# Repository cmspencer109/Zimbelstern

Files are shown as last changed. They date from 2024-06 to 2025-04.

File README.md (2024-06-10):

# The St. Martin Luther Zimbelstern

A MIDI-enabled zimbelstern for organs without one.

<div style="display: flex; justify-content: space-between;">
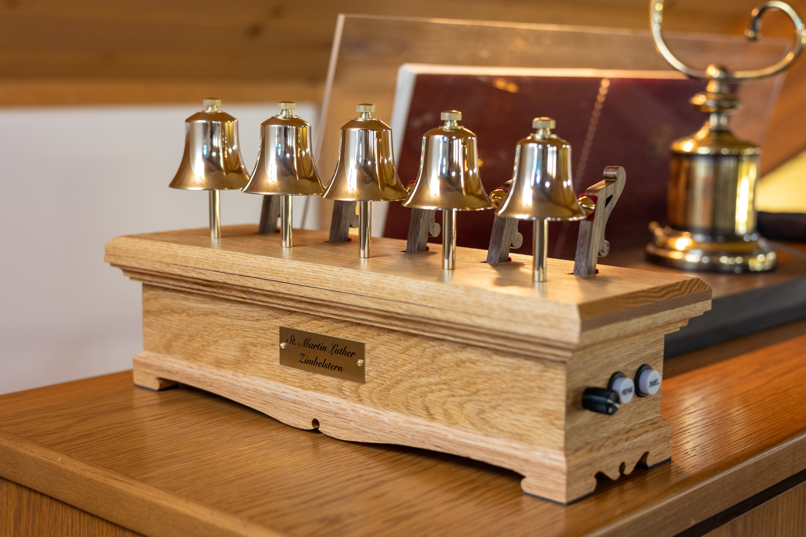
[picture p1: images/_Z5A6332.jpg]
  
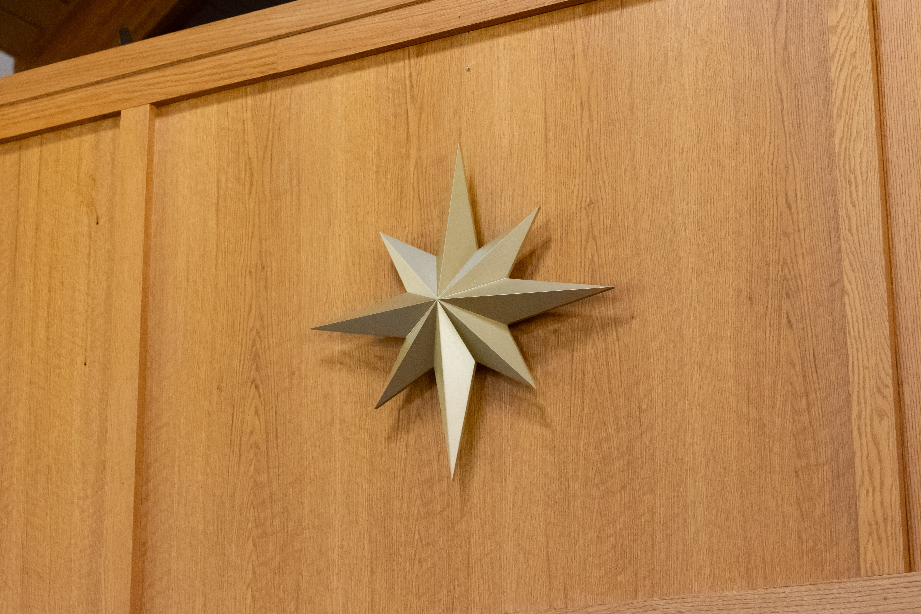
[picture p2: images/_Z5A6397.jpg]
   
</div>
<br>
This repo contains the code, schematics, and cad design files for the St. Martin Luther Zimbelstern.

## Design Overview

The St. Martin Luther Zimbelstern is an instrument designed for organs without a zimbelstern built into them. It features a solid oak case which fits comfortably on top of the organ console, allowing the controls to be in easy reach of the organist. In addition to a traditional Zimbel button for starting and stopping the zimbelstern, the St. Martin Luther Zimbelstern features a Prepare button which, when connected to a supported organ via MIDI, can identify when an organist begins playing the keyboards and automatically starts the zimbelstern.

Unlike more traditional designs which employ a rotating mechanism to strike a series of bells, this design allows for each bell to be played individually. Each bell is struck with a hammer which is actuated with an electromagnet. This allows the bells to be played at random, rather than in a predefined repeating sequence, as well as allowing adjustment over the speed and volume of the ringing. The electromagnets are controlled by a Raspberry Pi Pico microcontroller which lies at the heart of the zimbelstern, and is responsible for the entire operation of the zimbelstern.

The instrument uses 5 tuned Malmark handbells which form the D minor pentatonic scale. The pitches are D7, F7, G7, A7, and C8.

### MIDI Integration

The St. Martin Luther Zimbelstern has a MIDI IN port which can be connected to the MIDI OUT on a supported organ. The MIDI connection is only one-way, which means the zimbelstern only listens to the organ and does not talk back.

The MIDI connection is used for the Prepare button, which, when engaged will listen for "Note On" MIDI messages from the organ. When one of these messages is received, the microcontroller knows the organist has begun playing and will automatically start the zimbelstern.

Additionally, the MIDI connection is used to determine if any stops are engaged on the organ. This way, if the organist has pressed the Prepare button on the zimbelstern, but not yet engaged a registration on the organ, the zimbelstern will not start from an accidental silent key press. This functionality reads System Exclusive MIDI messages to identify if any stops are activated*, however, these are unique per organ manufacturer. As a result, the Prepare button will only work on Rodgers organs or any organ that uses the Rodgers/Roland SysEx message format. Support for other organs can be added by adding logic to read their SysEx message format.

*If the zimbelstern is plugged in after the organ is turned on, a stop change needs to be made on the organ to trigger a SysEx message so the zimbelstern can know the current state of the organ.

## Electronics

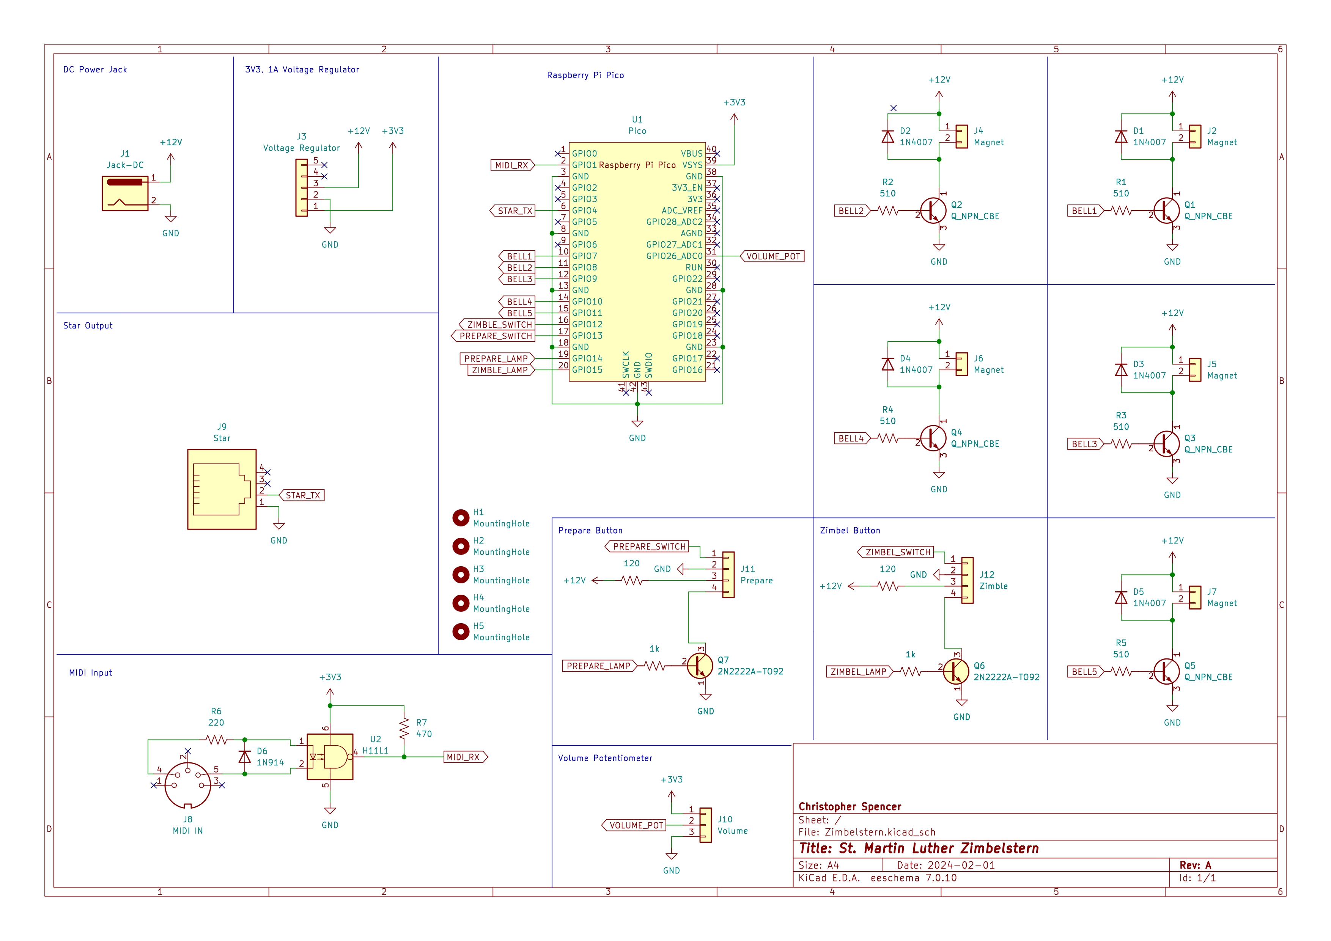
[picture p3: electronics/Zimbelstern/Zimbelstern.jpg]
Zimbelstern Schematic


### Circuit Board

* [JLCPCB](https://jlcpcb.com/) was used to order the PCB. The folder `Zimbel-2024-03-03` contains a KiCad export of all the files needed to order a new board from a PCB fabricator.

## Meaning Behind the Name

The name "St. Martin Luther Zimbelstern" reflects several key points about this zimbelstern. It is named after the great reformer Martin Luther who is remembered as we celebrate various 500-year anniversaries of Luther's work during the time of the reformation. Second, since the sound of the zimbelstern often signifies the song of heaven, the additional title of "St." reminds us that we are joined with Martin Luther and all those who are saints in heaven by Jesus' blood. Third, this zimbelstern was designed and built specifically for Martin Luther Church in Sunset Hills, Missouri whose name is also reflected in this name.

## Known Design Flaws

This zimbelstern was developed rapidly over 6 months and has some flaws. Below is a list of things that should be improved in future versions:

* Hammers produce an undesirable clacking sound when striking the bell
  * This is caused by a number of reasons, and may not be fixable without changing the hammer mechanism entirely.
  * The clearest bell rings occur when the striking object makes contact for the shortest amount of time possible. The longer the striking object remains on the bell, the more muted the tone will become until it doesn't ring at all. This is the first issue. The electromagnets cannot move the hammers fast enough. One solution is to reduce the weight of the hammers so they can swing faster. A better solution would be to use a mechanism similar to a grandfather clock, where the hammer is pulled back and springs forward to strike the bell.
  * The second issue is that the wooden hammer is absorbing some of the vibrations when striking and the wood is producing a dull echoing sound. Loosening the brass hammer head and adding a felt pad between the wooden hammer has helped to reduce this, but does not solve it entirely. One solution is to build the hammers out of a different material, such as all brass.
* ZIMBEL piston lamp voltage not properly regulated
  * The piston lamps operate at 5v, and are said to be used with a series resistor in Rodgers organs. This same type of series resistor configuration was used in the zimbelstern circuit to reduce the main 12v source to 5v. However, since the electromagnets also draw from the main 12v source a flickering in the piston lamp is produced when the zimbelstern is ringing.
  * One solution is to properly regulate the 12v to 5v using a buck converter. In the production model, the series resistor was removed and an extra buck converter wired in place. A proper fix would build this into the PCB.

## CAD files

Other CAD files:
electronics/Zimbelstern/KiCad-RP-Pico/SketchUp Model/Pico.skp
fusion360/P25-20 Bracket.f3d
fusion360/Pot Shaft Extender.f3d
fusion360/Potentiometer Bracket.f3d
fusion360/Rod Mount.f3d
fusion360/Star Motor Mount.f3d
fusion360/Star.f3d

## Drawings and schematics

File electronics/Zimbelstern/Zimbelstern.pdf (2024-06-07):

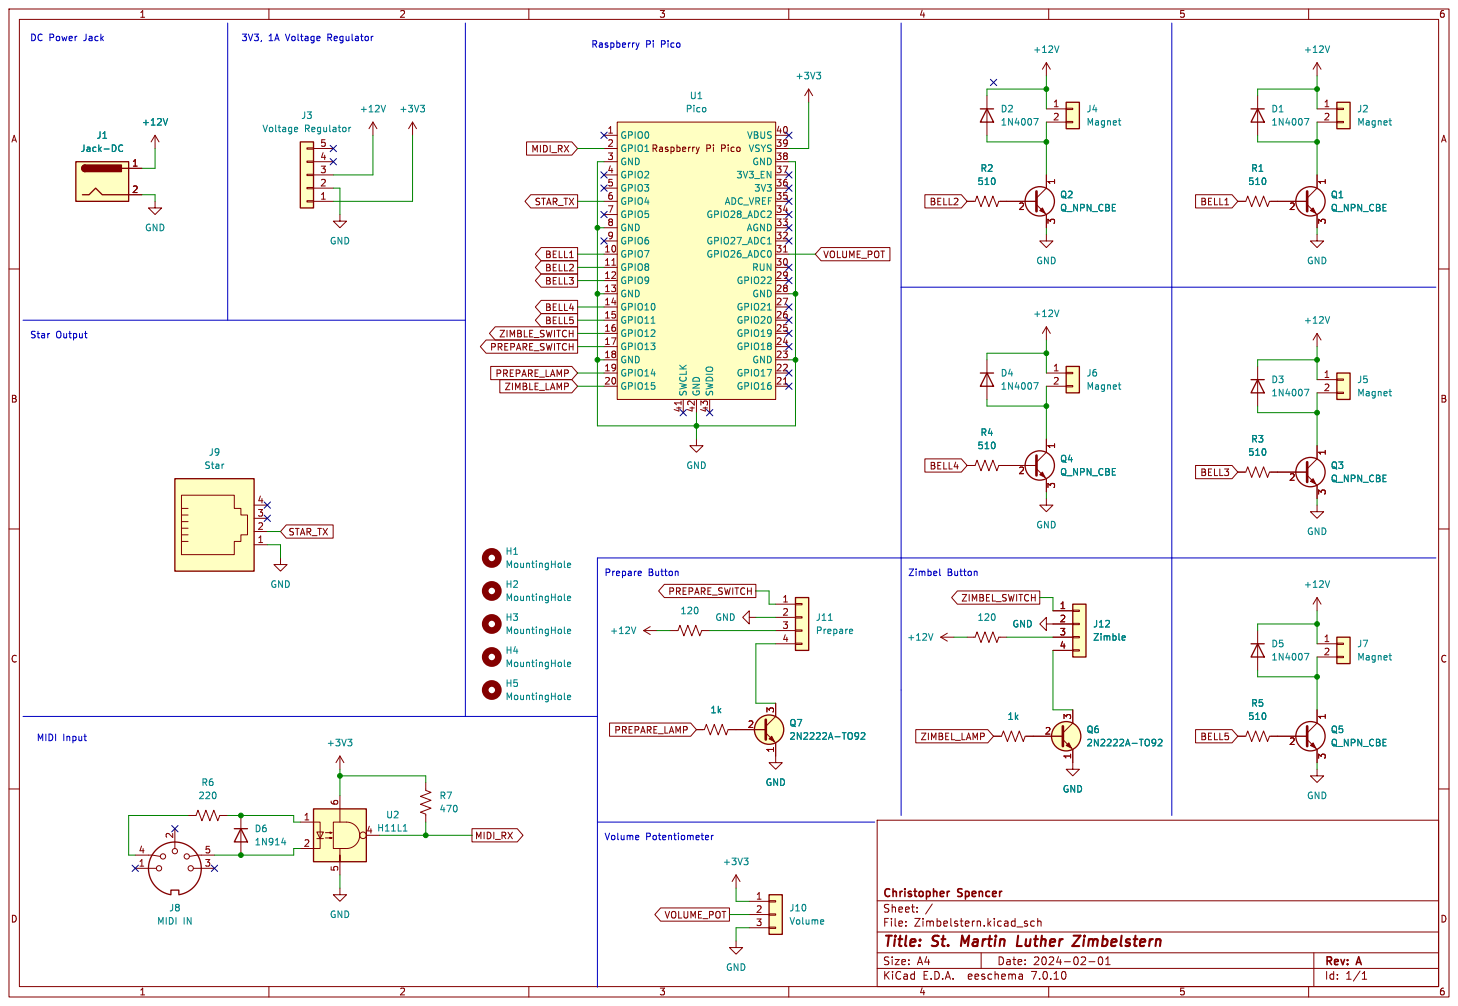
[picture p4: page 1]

3V3, 1A Voltage Regulator Star Output

File: Zimbelstern.kicad_sch Sheet: / Christopher Spencer GND

Volume Potentiometer MIDI Input

Id: 1/1 Title: St. Martin Luther Zimbelstern

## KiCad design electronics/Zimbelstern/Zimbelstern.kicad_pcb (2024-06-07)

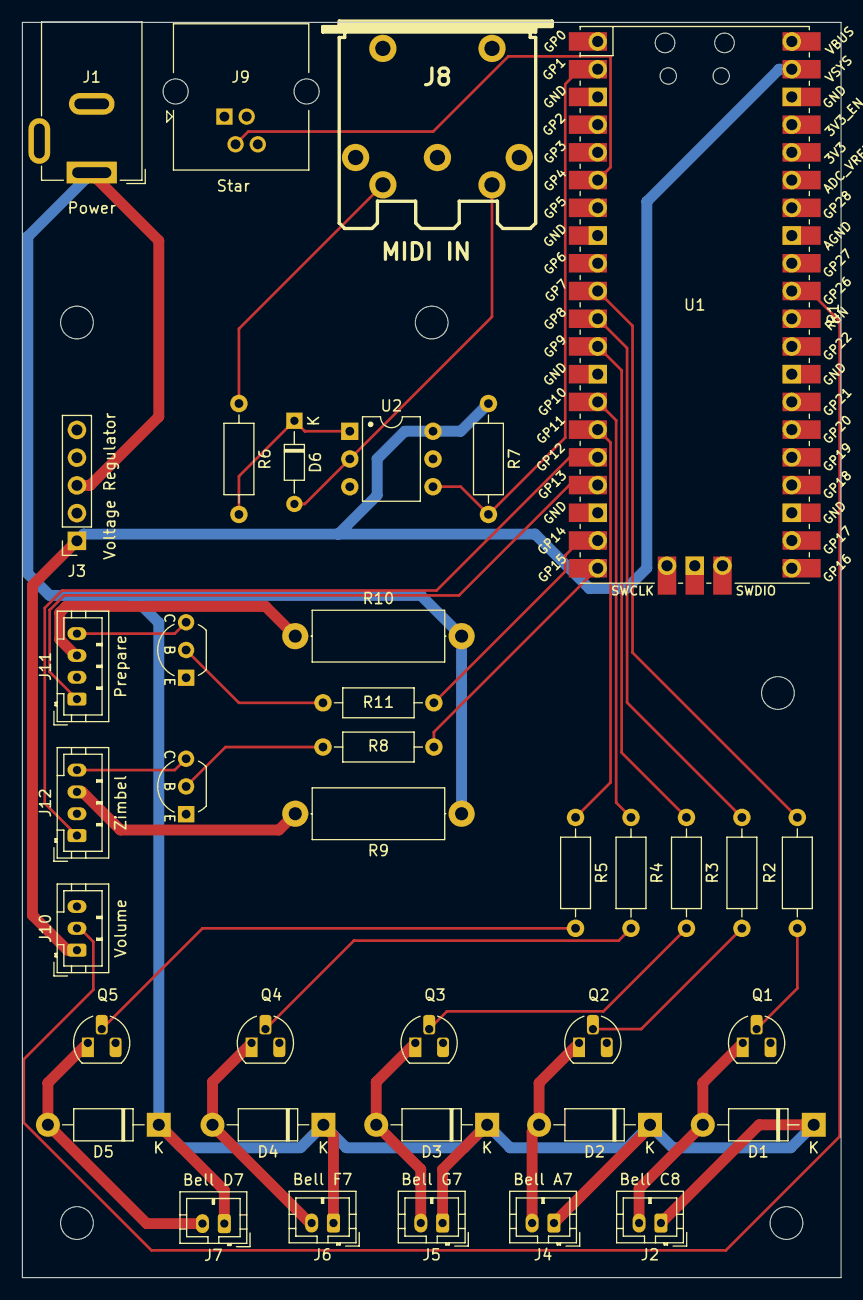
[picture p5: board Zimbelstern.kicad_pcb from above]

Board: 2 copper layers, 75.0 x 115.0 mm, 43 parts (0 on the bottom side), 34 nets.

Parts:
D1, D2, D3, D4, D5: 1N4007; D_DO-41_SOD81_P10.16mm_Horizontal
D6: 1N914; D_DO-34_SOD68_P7.62mm_Horizontal
H1, H2, H3, H4, H5: MountingHole; MountingHole_3mm
J1: Power; BarrelJack_GCT_DCJ200-10-A_Horizontal
J2: Bell C8; JST_PH_B2B-PH-K_1x02_P2.00mm_Vertical
J3: Voltage Regulator; PinSocket_1x05_P2.54mm_Vertical
J4: Bell A7; JST_PH_B2B-PH-K_1x02_P2.00mm_Vertical
J5: Bell G7; JST_PH_B2B-PH-K_1x02_P2.00mm_Vertical
J6: Bell F7; JST_PH_B2B-PH-K_1x02_P2.00mm_Vertical
J7: Bell D7; JST_PH_B2B-PH-K_1x02_P2.00mm_Vertical
J8: MIDI IN; MIDI_DIN5
J9: Star; RJ14_Connfly_DS1133-S4_Horizontal
J10: Volume; JST_PH_B3B-PH-K_1x03_P2.00mm_Vertical
J11: Prepare; JST_PH_B4B-PH-K_1x04_P2.00mm_Vertical
J12: Zimbel; JST_PH_B4B-PH-K_1x04_P2.00mm_Vertical
Q1, Q2, Q3, Q4, Q5: Q_NPN_CBE; TO-92_HandSolder
Q6, Q7: 2N2222A-TO92; TO-92_Inline_Wide_EBC
R1, R2, R3, R4, R5: 510; R_Axial_DIN0207_L6.3mm_D2.5mm_P10.16mm_Horizontal
R6: 220; R_Axial_DIN0207_L6.3mm_D2.5mm_P10.16mm_Horizontal
R7: 470; R_Axial_DIN0207_L6.3mm_D2.5mm_P10.16mm_Horizontal
R8, R11: 1k; R_Axial_DIN0207_L6.3mm_D2.5mm_P10.16mm_Horizontal
R9, R10: 120; R_Axial_DIN0414_L11.9mm_D4.5mm_P15.24mm_Horizontal
U1: Pico; RPi_Pico_SMD_TH
U2: H11L1; DIP-6_W7.62mm

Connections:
+3V3: J3.1, J10.1, R7.1, U1.39 (VSYS), U2.6
+12V: D1.1 (K), D2.1 (K), D3.1 (K), D4.1 (K), D5.1 (K), J1.1, J2.1, J3.3, J4.1, J5.1, J6.1, J7.1, R9.1, R10.1
BELL1: R1.1, U1.10 (GPIO7)
BELL2: R2.1, U1.11 (GPIO8)
BELL3: R3.1, U1.12 (GPIO9)
BELL4: R4.1, U1.14 (GPIO10)
BELL5: R5.1, U1.15 (GPIO11)
GND: J1.2, J3.2, J9.1, J10.3, J11.2, J12.2, Q1.3 (E), Q2.3 (E), Q3.3 (E), Q4.3 (E), Q5.3 (E), Q6.1 (E), Q7.1 (E), U1.3 (GND), U1.8 (GND), U1.13 (GND), U1.18 (GND), U1.23 (GND), U1.28 (GND), U1.38 (GND), U1.42 (GND), U2.5
MIDI_RX: R7.2, U1.2 (GPIO1), U2.4
unnamed: D1.2 (A), J2.2, Q1.1 (C)
unnamed: D2.2 (A), J4.2, Q2.1 (C)
unnamed: D3.2 (A), J5.2, Q3.1 (C)
unnamed: D4.2 (A), J6.2, Q4.1 (C)
unnamed: D5.2 (A), J7.2, Q5.1 (C)
unnamed: D6.2 (A), J8.5, U2.2
unnamed: D6.1 (K), R6.2, U2.1
unnamed: J8.4, R6.1
unnamed: J11.3, R10.2
unnamed: J11.4, Q7.3 (C)
unnamed: J12.3, R9.2
unnamed: J12.4, Q6.3 (C)
unnamed: Q1.2 (B), R1.2
unnamed: Q2.2 (B), R2.2
unnamed: Q3.2 (B), R3.2
unnamed: Q4.2 (B), R4.2
unnamed: Q5.2 (B), R5.2
unnamed: Q6.2 (B), R8.2
unnamed: Q7.2 (B), R11.2
PREPARE_LAMP: R11.1, U1.19 (GPIO14)
PREPARE_SWITCH: J11.1, U1.17 (GPIO13)
STAR_TX: J9.2, U1.6 (GPIO4)
VOLUME_POT: J10.2, U1.31 (GPIO26_ADC0)
ZIMBLE_LAMP: R8.1, U1.20 (GPIO15)
ZIMBLE_SWITCH: J12.1, U1.16 (GPIO12)

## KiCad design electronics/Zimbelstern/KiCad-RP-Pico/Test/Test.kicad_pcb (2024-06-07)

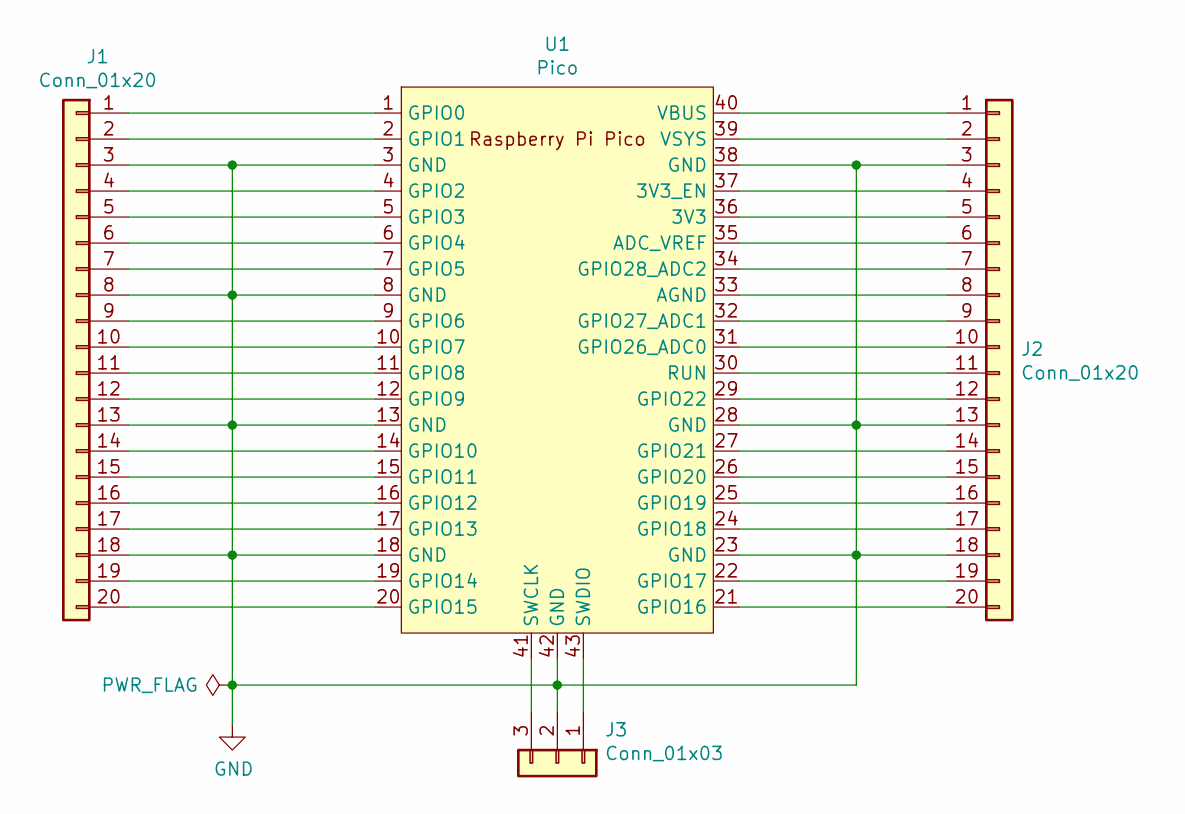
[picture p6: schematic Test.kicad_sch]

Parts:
J1, J2: Conn_01x20; PinSocket_1x20_P1.00mm_Vertical
J3: Conn_01x03; PinSocket_1x03_P1.00mm_Vertical
U1: Pico; RPi_Pico_SMD_TH

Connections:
GND: J1.3, J1.8, J1.13, J1.18, J2.3, J2.13, J2.18, J3.2, U1.3 (GND), U1.8 (GND), U1.13 (GND), U1.18 (GND), U1.23 (GND), U1.28 (GND), U1.38 (GND), U1.42 (GND)
unnamed: J1.1, U1.1 (GPIO0)
unnamed: J1.2, U1.2 (GPIO1)
unnamed: J1.4, U1.4 (GPIO2)
unnamed: J1.5, U1.5 (GPIO3)
unnamed: J1.6, U1.6 (GPIO4)
unnamed: J1.7, U1.7 (GPIO5)
unnamed: J1.9, U1.9 (GPIO6)
unnamed: J1.10, U1.10 (GPIO7)
unnamed: J1.11, U1.11 (GPIO8)
unnamed: J1.12, U1.12 (GPIO9)
unnamed: J1.14, U1.14 (GPIO10)
unnamed: J1.15, U1.15 (GPIO11)
unnamed: J1.16, U1.16 (GPIO12)
unnamed: J1.17, U1.17 (GPIO13)
unnamed: J1.19, U1.19 (GPIO14)
unnamed: J1.20, U1.20 (GPIO15)
unnamed: J2.1, U1.40 (VBUS)
unnamed: J2.2, U1.39 (VSYS)
unnamed: J2.4, U1.37 (3V3_EN)
unnamed: J2.5, U1.36 (3V3)
unnamed: J2.6, U1.35 (ADC_VREF)
unnamed: J2.7, U1.34 (GPIO28_ADC2)
unnamed: J2.8, U1.33 (AGND)
unnamed: J2.9, U1.32 (GPIO27_ADC1)
unnamed: J2.10, U1.31 (GPIO26_ADC0)
unnamed: J2.11, U1.30 (RUN)
unnamed: J2.12, U1.29 (GPIO22)
unnamed: J2.14, U1.27 (GPIO21)
unnamed: J2.15, U1.26 (GPIO20)
unnamed: J2.16, U1.25 (GPIO19)
unnamed: J2.17, U1.24 (GPIO18)
unnamed: J2.19, U1.22 (GPIO17)
unnamed: J2.20, U1.21 (GPIO16)
unnamed: J3.1, U1.43 (SWDIO)
unnamed: J3.3, U1.41 (SWCLK)

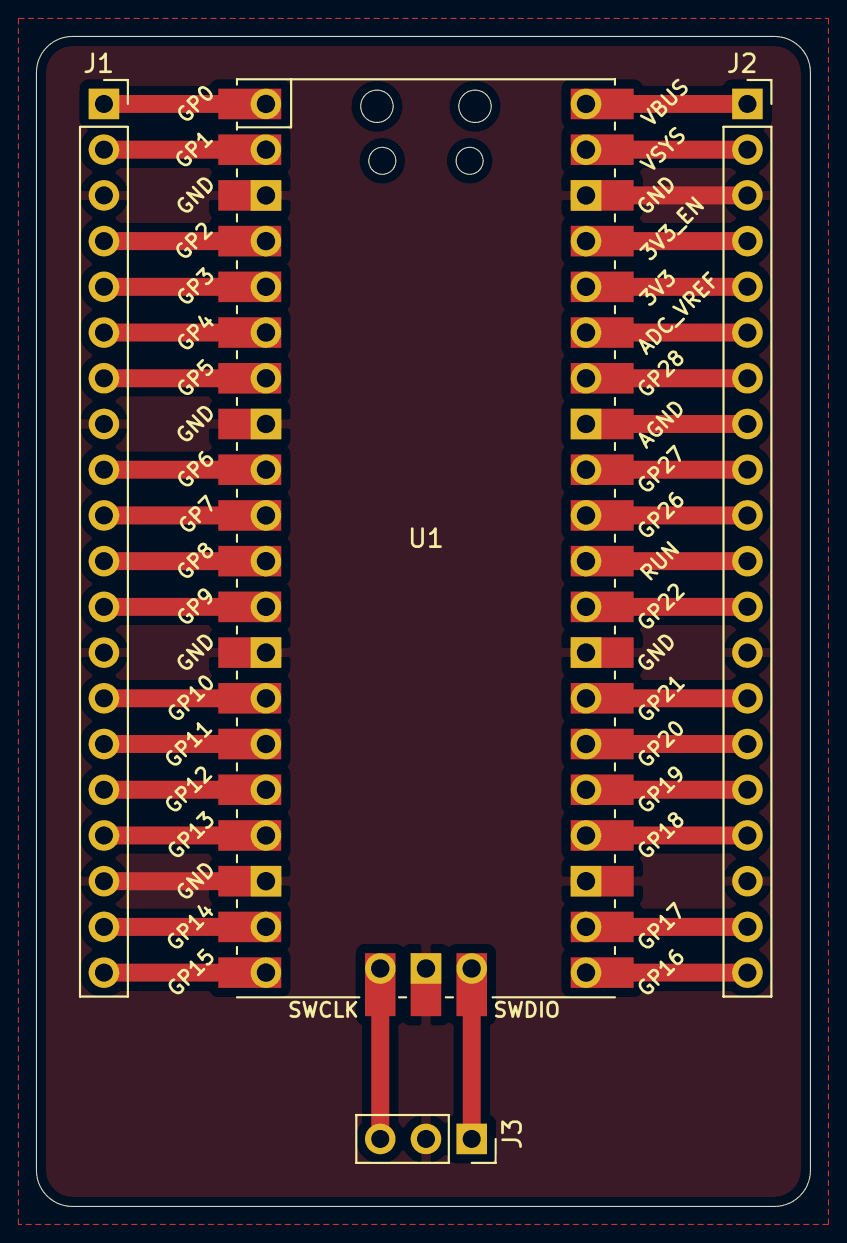
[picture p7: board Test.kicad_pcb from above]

Board: 2 copper layers, 43.0 x 65.0 mm, 4 parts (0 on the bottom side), 36 nets.

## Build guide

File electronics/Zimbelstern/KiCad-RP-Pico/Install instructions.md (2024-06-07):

# Install instructions

## 1. Copy the files locally

Copy the `RP-Pico Libraries` folder wherever you like on your computer.

## 2. Install the Raspberry Pi Pico board schema symbol

Use the `KiCad | Preferences | Manage Symbol Libraries...` command to manage the symbol library:

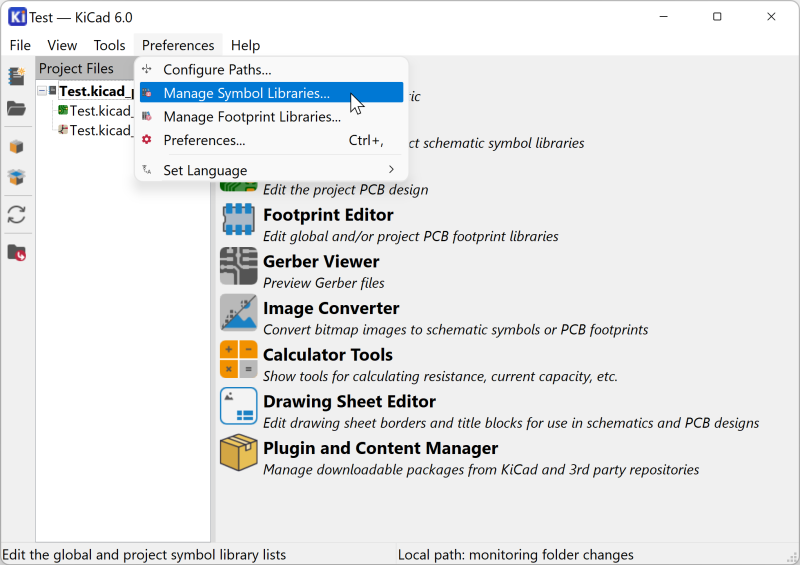
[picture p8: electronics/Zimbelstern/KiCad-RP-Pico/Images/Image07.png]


then select the global tab and click on the folder button:

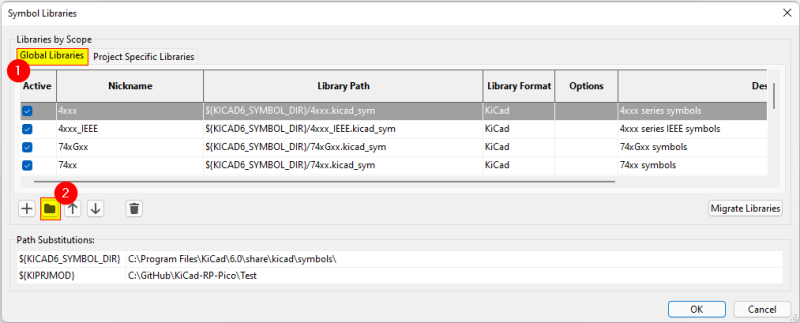
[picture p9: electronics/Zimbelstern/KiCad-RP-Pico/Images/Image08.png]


navigate to the `RP-Pico Libraries` folder, select the `MCU_RaspberryPi_and_Boards.kicad_sym` file and open it:

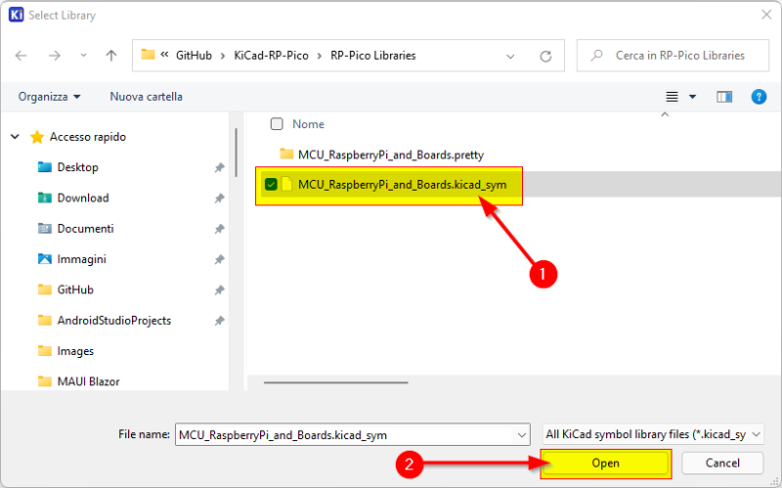
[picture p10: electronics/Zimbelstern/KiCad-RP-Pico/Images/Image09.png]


et voilà, the first step is completed:

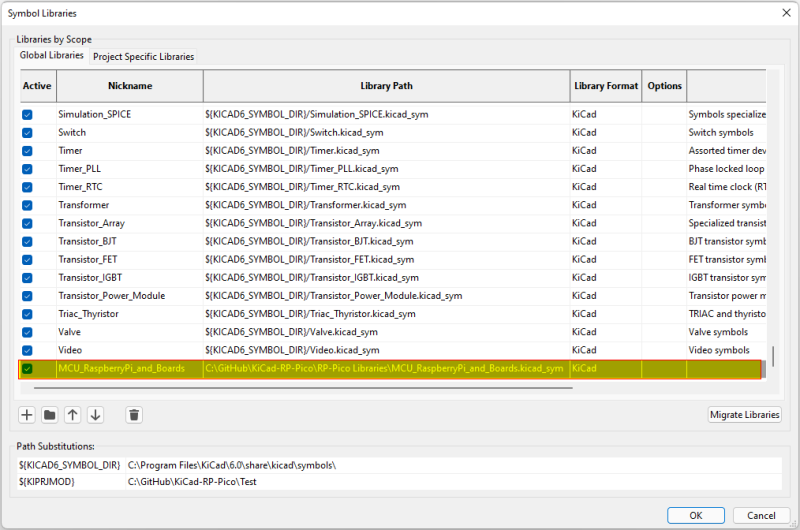
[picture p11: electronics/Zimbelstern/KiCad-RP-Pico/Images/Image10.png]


You can now close the symbol libraries manager window.

## 3. Install the Raspberry Pi Pico board footprint

You can use a similar approach to add the footprint to the footprint libraries manager, but I've found some issues that I've solved using the footprint editor, so here are the steps I suggest you to follow:

Open the footprint editor

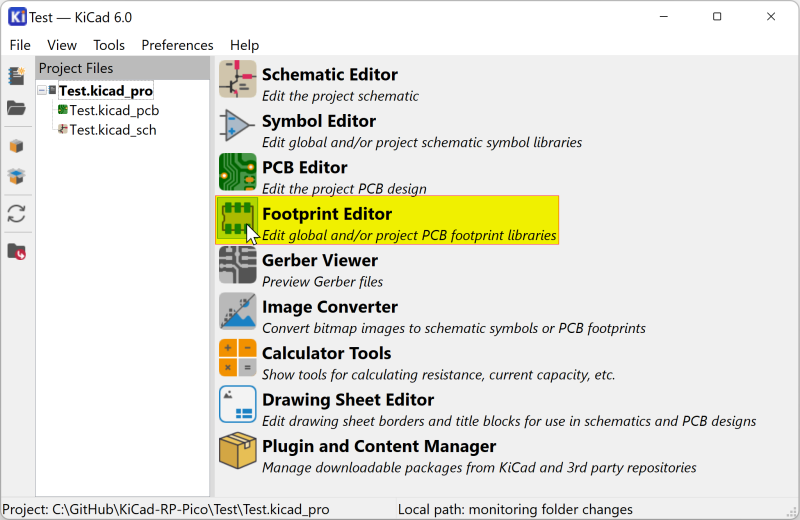
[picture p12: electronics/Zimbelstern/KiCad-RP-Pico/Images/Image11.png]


wait for the footprints to load... then use the `File | Add Library` command:

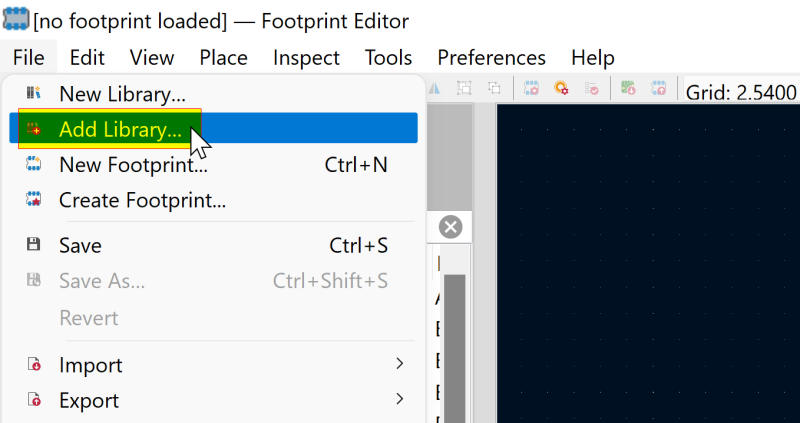
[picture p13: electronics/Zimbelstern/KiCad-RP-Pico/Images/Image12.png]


confirm the `Global` choice:

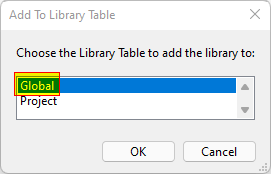
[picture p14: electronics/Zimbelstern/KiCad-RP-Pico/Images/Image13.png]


and select the `MCU_RaspberriPi_and_Boards.pretty` folder (yes, the folder represent a footprint library on KiCad):

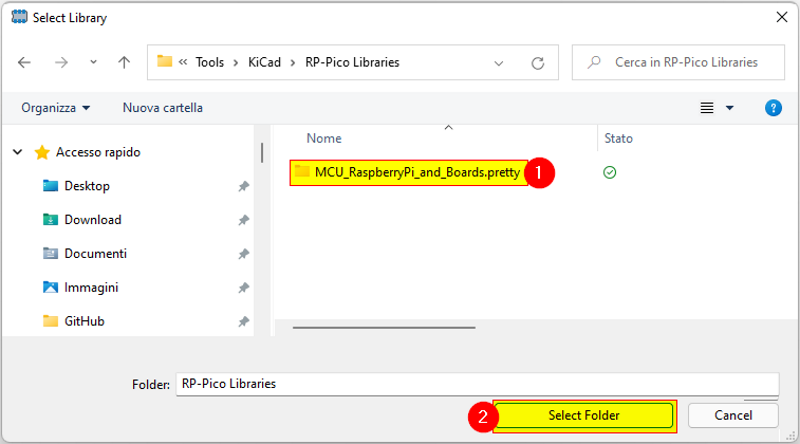
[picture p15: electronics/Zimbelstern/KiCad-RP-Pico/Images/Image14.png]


Now the library is installed on KiCad with the Raspberry Pi Pico footprint (double click on it to see it on the editor pane):

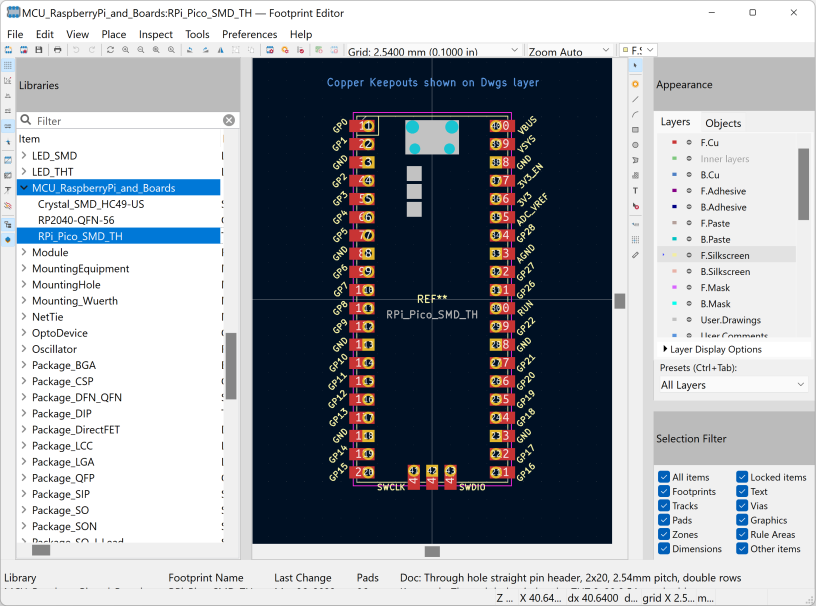
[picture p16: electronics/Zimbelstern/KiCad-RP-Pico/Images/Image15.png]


Don't close the windows as the next step start from here.

## 4. Install the Raspberry Pi Pico board footprint 3D visual

If not already open, open the the footprint editor

symbol library manager

double click on the `RPi_Pico_SMD_TH` footprint from the `MCU_RaspberriPi_and_Boards` library and then click on the `Footprint properties` icon:

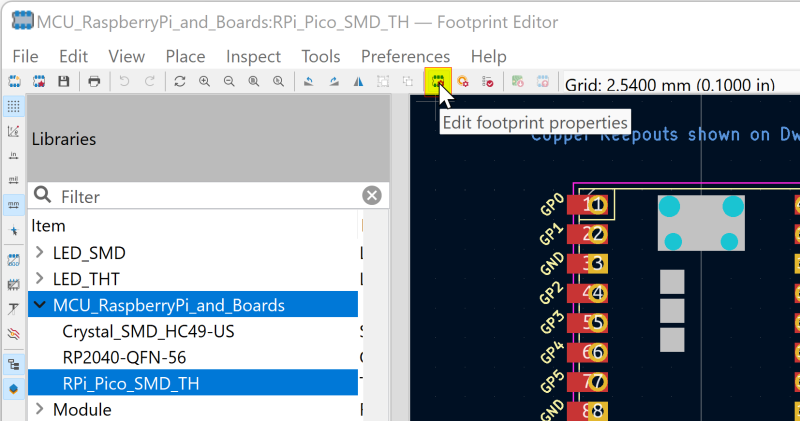
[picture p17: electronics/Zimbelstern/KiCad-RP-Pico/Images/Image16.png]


In the footprint properties window, first select the `3D Settings` tab. Please note that the preview shows only the PCB board with the footprint added on step 3, without any 3D representation of the Raspberry Pi Pico board. Now click on the folder icon to add the 3D model:

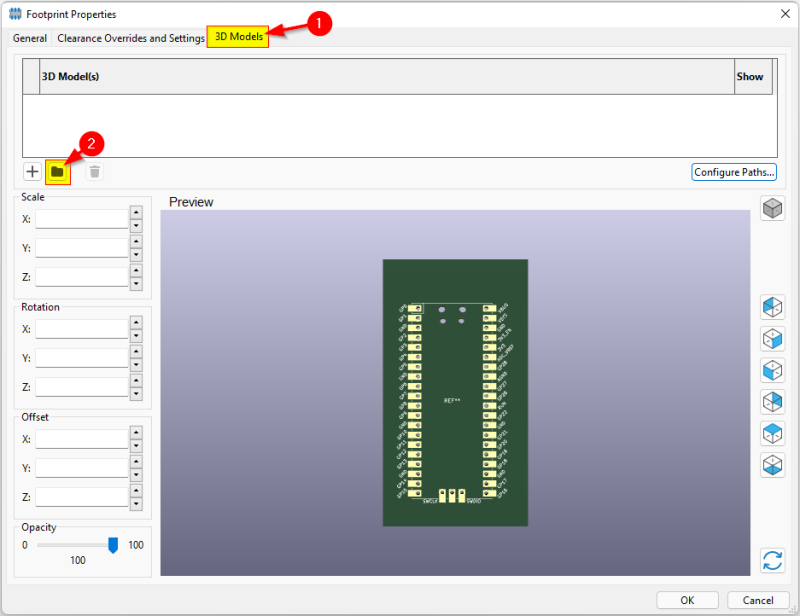
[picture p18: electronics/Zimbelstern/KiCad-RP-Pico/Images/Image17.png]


Navigate to the `RP-Pico Libraries` folder, select the `Pico.wrl` file and wait until the model is shown in the right panel, then confirm with OK:

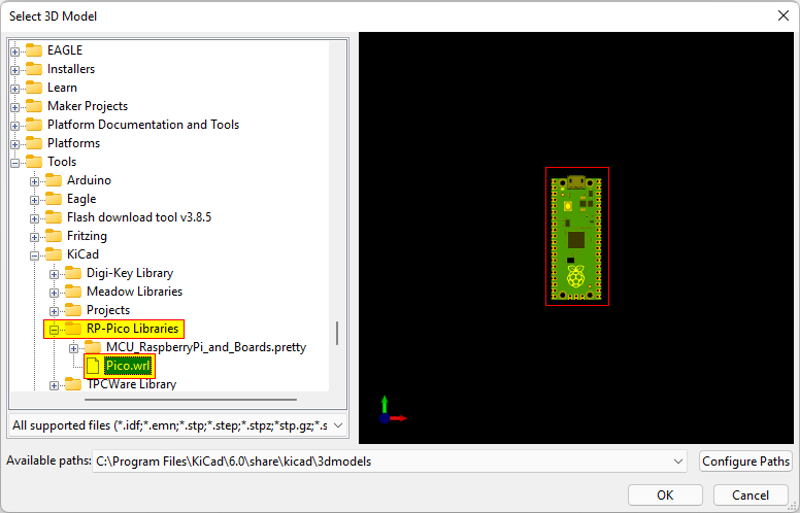
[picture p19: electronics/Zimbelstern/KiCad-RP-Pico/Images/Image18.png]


The model is already scaled and translated to match the footprint:

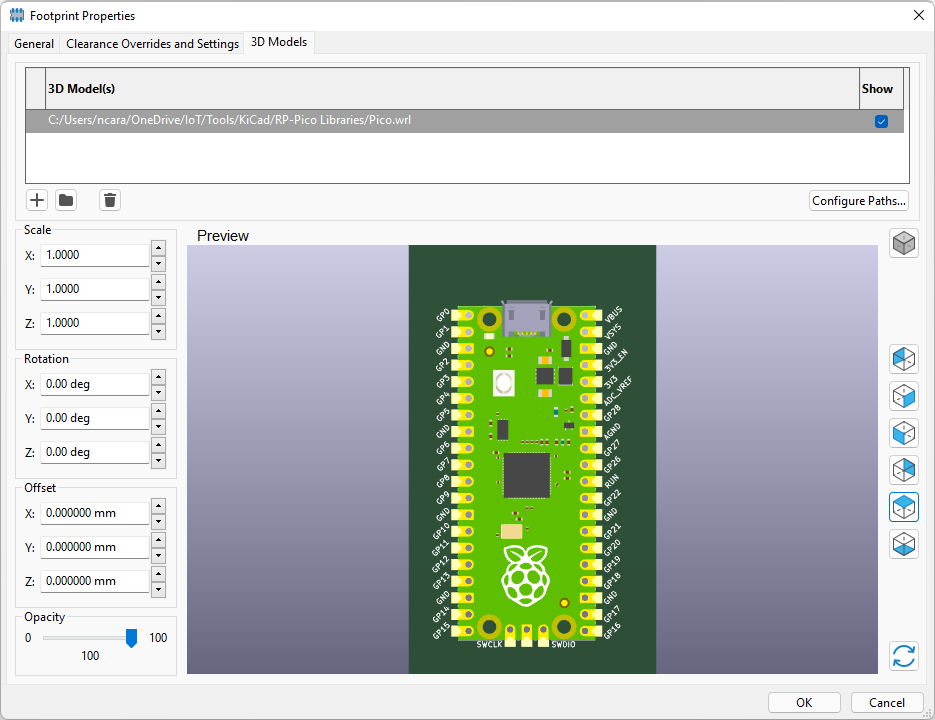
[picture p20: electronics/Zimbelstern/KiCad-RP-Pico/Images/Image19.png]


now close the `Footprint Properties` window, and the `Footprint Editor`, obviously saving the changes.

## Conclusion

Now that you've installed the schema and footprint and added the 3D model to the footprint, you can use the Raspberry Pi Pico board on your KiCad projects.

I've also added a test KiCad Project on the `Test` folder, that you can use to see an example of it.

Have fun!

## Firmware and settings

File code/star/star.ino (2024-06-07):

/*
The following program is intended for use with the Zimbelstern Star of Martin Luther Church, Sunset Hills, MO.
The program receives on and off communications, as well as speed values via a serial connection.

Bytes should be streamed to the device at minimum more than once per second. If the device does not receive communication 
after 1 second, it will shut off on its own. This is to prevent a runaway uncontrolled process in case of a connection failure.

Bytes are sent in hex form, where the upper nibble should be high (F) to indicate that it should turn on. 
The lower nibble 0 - F maps to the min and max speed constants defined below.

Examples:
0xF0 - Run at the slowest speed
0xF8 - Run at a medium speed
0xFF - Run at the maximum speed
0x00 - Doesn't do anything because the upper nibble is not high

*/

#include <AccelStepper.h>

// Define pins
#define ENABLE_PIN 2
#define STEP_PIN 3
#define DIRECTION_PIN 4

const int MIN_SPEED = 1000;
const int MAX_SPEED = 5000;
const int STARTING_ACCELERATION = 1000;
const int STOPPING_ACCELERATION = 750;

const int STEPS_IN_ONE_REVOLUTION = 6400; // 1600 steps * 4 pulley ratio

unsigned long lastByteReceivedTime = 0;
bool motorRunning = false;

AccelStepper stepper(AccelStepper::DRIVER, STEP_PIN, DIRECTION_PIN);

void setup() {
  // Set the pins
  pinMode(ENABLE_PIN, OUTPUT);
  pinMode(DIRECTION_PIN, OUTPUT);
  pinMode(STEP_PIN, OUTPUT);

  // Set the maximum speed and acceleration
  stepper.setMaxSpeed(MAX_SPEED);

  // Initialize Serial communication
  Serial.begin(9600);
}

void startMotor(int speed) {
  stepper.setAcceleration(STARTING_ACCELERATION);

  if (motorRunning == true) {
    return;
  }

  digitalWrite(ENABLE_PIN, LOW); // Low is on
  stepper.setMaxSpeed(speed);
  stepper.move(-2147483647); // Set the largest possible position. Multiply by -1 to change direction.
  motorRunning = true;
}

void stopMotor() {
  stepper.stop();
  motorRunning = false;
}

// Stops the motor on the closest quarter revolution with full deceleration
void stopMotorOnQuarter() {
  /* stepper.stop() updates the target position to the point at which it will stop
     based on the current speed and rate at which it will slow down.
     We then add to this number the smallest amount needed to make it divisble by
     the number of steps in a quarter revolution, and move to this new position.
  */
  stepper.setAcceleration(STOPPING_ACCELERATION);
  stepper.stop();
  long targetPosition = stepper.targetPosition();
  int stepsInQuarterRevolution = STEPS_IN_ONE_REVOLUTION / 4;
  long targetPositionToEndOnAQuarter = targetPosition - (stepsInQuarterRevolution + (targetPosition % -stepsInQuarterRevolution));
  stepper.moveTo(targetPositionToEndOnAQuarter);
  motorRunning = false;
}

void loop() {
  // Check if data is available on Serial
  if (Serial.available() > 0) {

    byte receivedByte = Serial.read();
    // Serial.println(receivedByte); // TESTING ONLY, DO NOT USE IN PRODUCTION

    // Extract upper nibble for control and lower nibble for speed
    byte control = (receivedByte & 0xF0) >> 4;
    byte speedValue = receivedByte & 0x0F;

    // Map 0 - F to the min and max speeds so sender can control the speed
    int speed = map(speedValue, 0, 15, MIN_SPEED, MAX_SPEED);

    // Check the upper nibble for control
    if (control == 0x0F) {
      startMotor(speed);
    }
    
    // Update last byte received time
    lastByteReceivedTime = millis();
  }

  // Stop the motor if no bytes received for 100 ms
  if (millis() - lastByteReceivedTime > 50 && motorRunning) {
    // Choose how you want to stop the motor
    // stopMotor();
    stopMotorOnQuarter();
  }

  // Run the stepper motor
  stepper.run();

  // Disable stepper driver when motor is not turning to save power
  if (!stepper.isRunning() && !motorRunning) {
    digitalWrite(ENABLE_PIN, HIGH); // High is off
  }
}

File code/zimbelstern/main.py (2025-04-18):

import uasyncio
import time
import random
from machine import Pin, UART, ADC


# If a melody is not specified, a random melody will be played
DELAY_BETWEEN_MELODY_REPEAT = False
ZIMBEL_MELODY = ''
# ZIMBEL_MELODY = 'cdfgacgdcafgcadf' # 16 note pattern
# ZIMBEL_MELODY = 'dfgac' # ascending
# ZIMBEL_MELODY = 'cagfd' # descending 
# ZIMBEL_MELODY = 'dfgacagf' # ascending and descending

FADE_VOLUME_START = True
FADE_TEMPO_START = False
FADE_IN_DURATION = 1 # seconds
tempo = 300 # bpm
STARTING_TEMPO = tempo-60 # bpm
PLAY_SECOND_NOTE = True
SECOND_NOTE_DELAY = 30 # ms

# FOR DEBUGGING ONLY
# Set to False if needed for disabling certain features
# Set to True in production
BELLS_ENABLED = True
STAR_ENABLED = True


# Define board connections

bell_d = Pin(11, Pin.OUT)
bell_f = Pin(10, Pin.OUT)
bell_g = Pin(9, Pin.OUT)
bell_a = Pin(8, Pin.OUT)
bell_c = Pin(7, Pin.OUT)

bells = {
    'd': bell_d,
    'f': bell_f,
    'g': bell_g,
    'a': bell_a,
    'c': bell_c
}

note_weights = {key: 1 for key in bells.keys()}

midi_uart = UART(0, baudrate=31250, tx=Pin(0), rx=Pin(1))
star_uart = UART(1, baudrate=9600, tx=Pin(4))

prepare_button = Pin(13, Pin.IN, Pin.PULL_UP)
prepare_button_lamp = Pin(14, Pin.OUT)
prepare_button_state = False

zimbel_button = Pin(12, Pin.IN, Pin.PULL_UP)
zimbel_button_lamp = Pin(15, Pin.OUT)
zimbel_button_state = False

volume_knob = ADC(26)
volume = 0

beats_per_second = tempo // 60
num_beats_to_fade = int(beats_per_second * FADE_IN_DURATION)
faded_volumes = []
faded_tempos = []


# Define and assign initial states

prepare_button_clock = -1
zimbel_state = False
zimbel_playing = False
zimbel_button_lamp.value(False)
zimbel_is_prepared = False
stops_on = False


# Define constants

# Used to debounce button presses (ms)
# Suggested range: 50-200
DEBOUNCE_TIME = 100

# Used to yield control to the event loop (ms)
YIELD_TIME = 1

# Set volume range of potentiometer
# Value is the amount of time each electromagnet is powered on for (ms)
ABSOLUTE_MIN_VOLUME = 10
MIN_VOLUME = 12
MAX_VOLUME = 20


def get_spread(min_value, max_value, num_steps):
    step = (max_value - min_value) / (num_steps - 1)
    return [min_value + step * i for i in range(num_steps)]


def zimbel_on():
    global zimbel_state, zimbel_button_lamp, faded_volumes, faded_tempos
    
    if not zimbel_state:
        faded_volumes = get_spread(ABSOLUTE_MIN_VOLUME, volume, num_beats_to_fade)
        faded_tempos = get_spread(STARTING_TEMPO, tempo, num_beats_to_fade)

        zimbel_state = True
        zimbel_button_lamp.value(True)
        print('Zimbel on')
        prepare_zimbel_off()


def zimbel_off():
    global zimbel_state, zimbel_playing, zimbel_button_lamp

    if zimbel_state:
        zimbel_state = False
        zimbel_playing = False
        zimbel_button_lamp.value(False)
        print('Zimbel off')
        prepare_zimbel_off()


def prepare_zimbel_on():
    global zimbel_is_prepared

    if not zimbel_is_prepared:
        zimbel_off()
        zimbel_is_prepared = True
        prepare_button_lamp.value(True)
        print('Prepare on')


def prepare_zimbel_off():
    global zimbel_is_prepared

    zimbel_is_prepared = False
    prepare_button_lamp.value(False)
    print('Prepare off')


def is_note_on(midi_bytes):
    if len(midi_bytes) < 3:
        return False

    # Check if the status byte indicates a Note On message
    if (midi_bytes[0] & 0xF0) == 0x90:
        # Check if the velocity is greater than 0
        if midi_bytes[2] > 0:
            return True

    return False


def is_sysex(message_bytes):
    if len(message_bytes) < 2:
        return False
    
    # Extract status bytes and check if it is the start or end of SysEx
    start_byte = message_bytes[0]
    end_byte = message_bytes[-1]
    
    if start_byte == 0xF0 and end_byte == 0xF7:
        return True
    
    return False


def all_stops_off_rodgers(input_bytes):
    rodgers_stops_bytes = input_bytes[7:-2]
    return all(byte == 0 for byte in rodgers_stops_bytes)


async def midi_loop():
    global zimbel_is_prepared, stops_on

    while True:
        if midi_uart.any():
            midi_bytes = list(midi_uart.read())
            
            # Filter out Active Sensing messages
            if midi_bytes == [0xFE]: continue
            # Strip out Active Sensing byte if it gets caught in another message
            if midi_bytes[0] == 0xFE: midi_bytes = midi_bytes[1:]

            # Process MIDI message:

            # If SysEx (Used by Rodgers organs to send stop state messages)
            # Used to read the state of the stops to see if stops are on or off
            if is_sysex(midi_bytes):
                # Only able to read Rodgers SysEx messages
                if all_stops_off_rodgers(midi_bytes):
                    stops_on = False
                else:
                    stops_on = True

            # If zimbel is prepared, stops are on, and a key is pressed
            if zimbel_is_prepared and stops_on and is_note_on(midi_bytes):
                print('Zimbel is prepared and note on')
                zimbel_on()

            # If general cancel
            if midi_bytes == [203, 19]:
                print('General Cancel')
                zimbel_off()
                stops_on = False
                continue

        # Yield control to event loop
        await uasyncio.sleep_ms(YIELD_TIME)


async def zimbel_button_loop():
    global zimbel_button_state, zimbel_state

    while True:
        if zimbel_button.value() == 0:  # Button is being pressed
            if not zimbel_button_state:
                #print('Button pressed')
                zimbel_button_state = True
                
                # Toggle zimbel state
                if zimbel_state:
                    zimbel_off()
                else:
                    zimbel_on()
                
                # Debounce after press
                await uasyncio.sleep_ms(DEBOUNCE_TIME)
            
        else:  # Button is not being pressed
            if zimbel_button_state:
                #print('Button released')
                zimbel_button_state = False
        
        # Yield control to event loop
        await uasyncio.sleep_ms(YIELD_TIME)
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

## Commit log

2024-01-10 Add support for ready button
2024-01-17 Fix zimbel ready feature to work with all types of note on off commands
    [zimbel_midi_ready.py]
2024-01-18 Proof of concept for binding to sysex
    [zimbel_midi_ready.py]
2024-01-25 Fix writing midi trigger bytes to file
    [zimbel_midi_ready.py]
2024-01-31 Update magnet test code for new circuit
2024-02-01 Integrate adjustment dials and code for triggering magnet
2024-02-08 Add stepper test
2024-02-11 Add star uart communication
2024-02-12 Star stepper motor tests
2024-02-16 Fix/Add working magnet loop to main zimbel program
    [zimbel_midi.py]
2024-02-22 Add arduino code for star
2024-03-15 Pin updates, fix star loop
    [zimbel.py]
2024-03-21 Star test conditional and print statements for testing
2024-03-26 Change zimbel toggle to work on button release
    Fixes zimbel starting to play when holding down zimbel button to enter program mode
    [zimbelstern.py]
2024-03-27 Add support for organ power on midi message (used for clearing midi trigger)
2024-03-28 Add micro pico VScode plugin configuration
2024-03-28 set stops to off with gc piston
2024-03-29 Add comment to fix
    [zimbelstern.py]
2024-03-30 Changes and fixes from organ testing on Good Friday
    [zimbelstern.py]
2024-03-30 Cleanup comments that were fixed and remove WIP code for volume fader
    [zimbelstern.py]
2024-03-30 Format of print messages
2024-03-30 Rename for board
2024-03-30 Fix bug where any possible midi trigger would activate the zimbelstern if it was unset
    [main.py]
2024-04-06 Reduce max volume, fix playing a note to not cancel activation mode, and increase star data rate
    [main.py]
2024-04-06 Disable pico led used for testing
2024-04-06 Add zimbel stats processer
    [zimbel_log_example.csv]
2024-06-02 WIP: removing digital bell player and midi trigger functionality
    [zimbel_log_example.csv]
2024-06-03 Change zimbel piston to start on press instead of release
2024-06-07 Adding kicad and fusion 360 files
    [P25-20 Bracket.f3d, Pico.skp, Pot Shaft Extender.f3d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]
